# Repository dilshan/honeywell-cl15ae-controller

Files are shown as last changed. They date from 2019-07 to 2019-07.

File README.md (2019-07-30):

# Replacement driver for Honeywell CL15AE

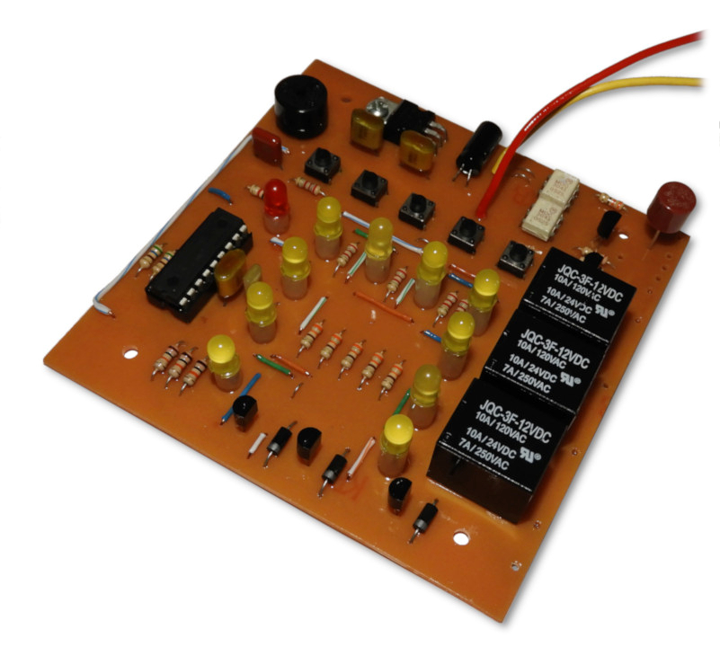
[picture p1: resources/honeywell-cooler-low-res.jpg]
Prototype version of the replacement board


PIC16F819 based replacement driver unit for Honeywell (JMTEK) CL15AE evaporative air cooler.

Detail posting about this project is available at [jayakody2000lk.blogspot.com](http://jayakody2000lk.blogspot.com/2019/07/replacement-driver-for-honeywell-cl15ae.html).

**WARNING:** This unit has a direct connection with the AC mains voltage and makes sure to take all necessary precautions while assembling, testing and installing this board. Improper connection or short-circuits would cause lethal shock or fire!

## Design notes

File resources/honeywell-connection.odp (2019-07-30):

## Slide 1

AC Mains Input

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
Main Motor

Swing Motor

Pump Motor

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
J5 / J7

J3 / J9

J13

J14

Control Board

PSU

N

L

Control board wiring diagram

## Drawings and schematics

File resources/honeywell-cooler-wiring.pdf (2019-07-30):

# Control Board

# Control board wiring diagram

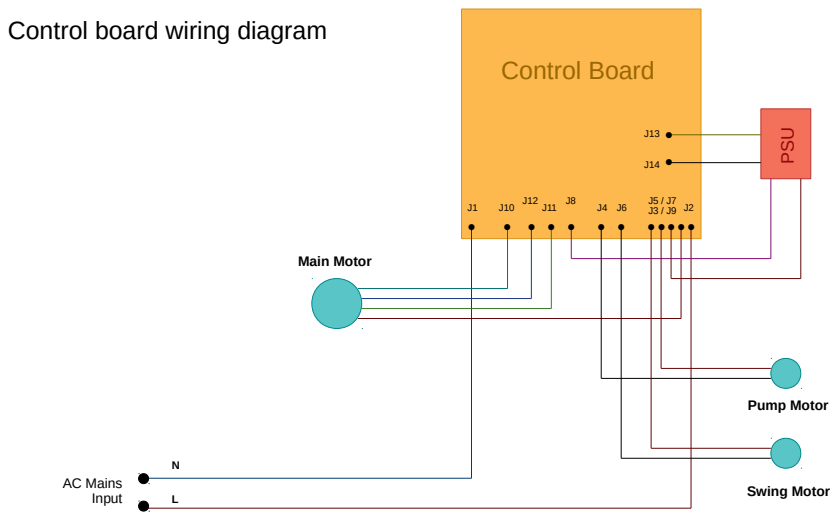
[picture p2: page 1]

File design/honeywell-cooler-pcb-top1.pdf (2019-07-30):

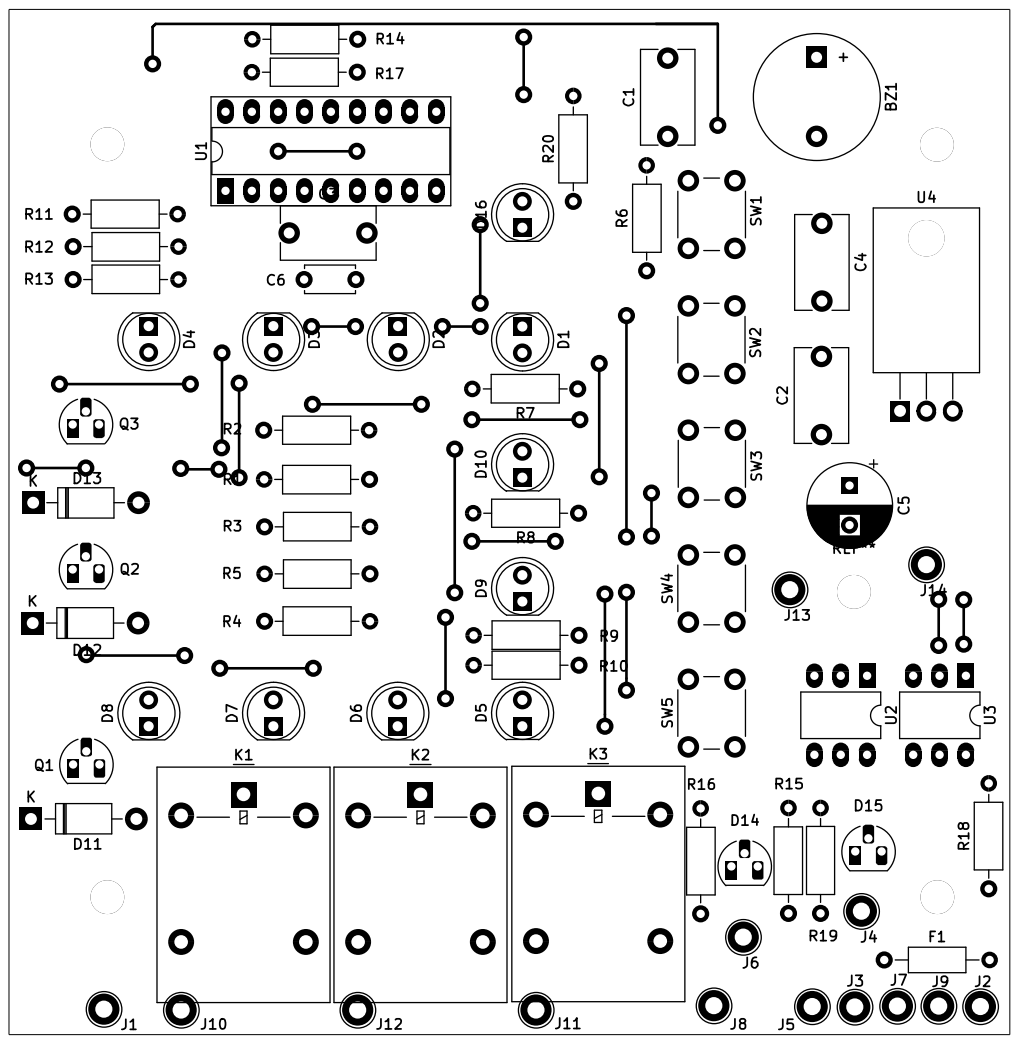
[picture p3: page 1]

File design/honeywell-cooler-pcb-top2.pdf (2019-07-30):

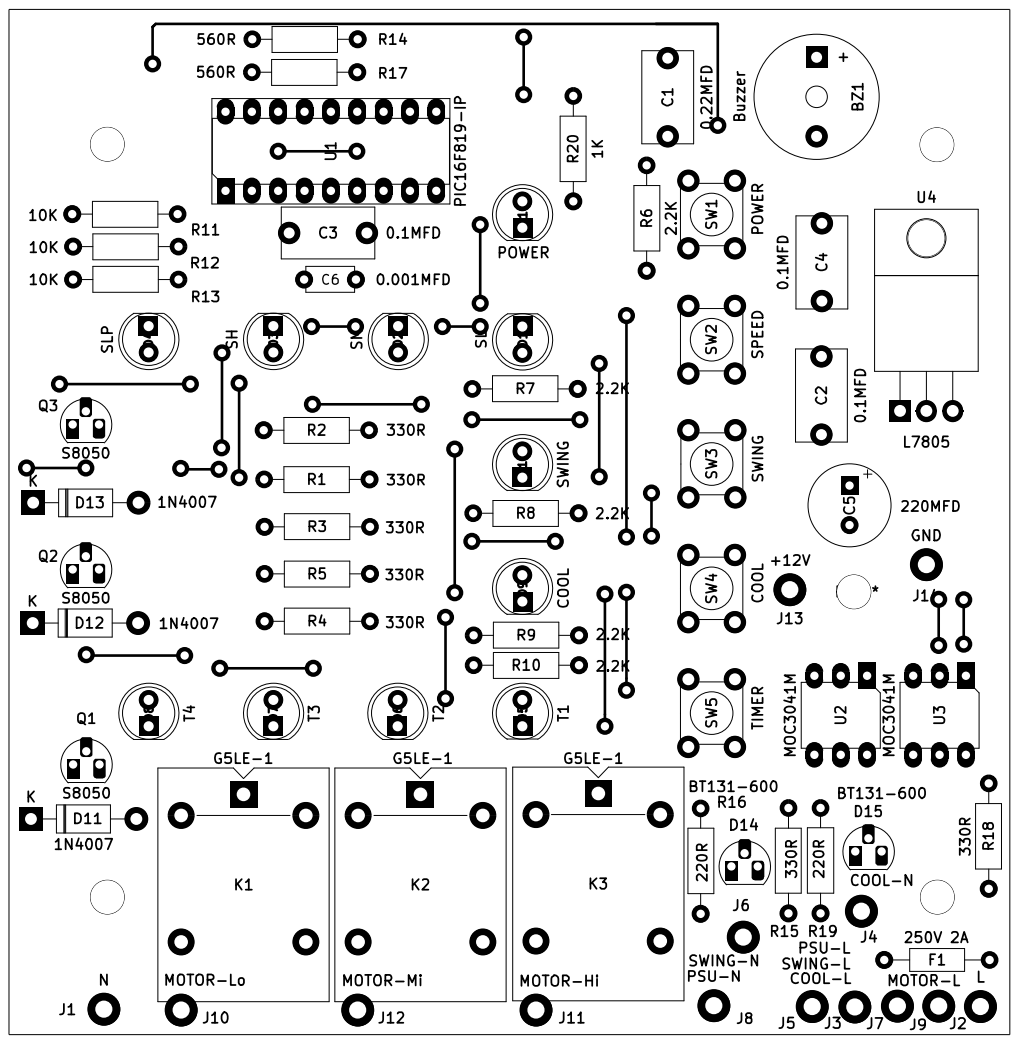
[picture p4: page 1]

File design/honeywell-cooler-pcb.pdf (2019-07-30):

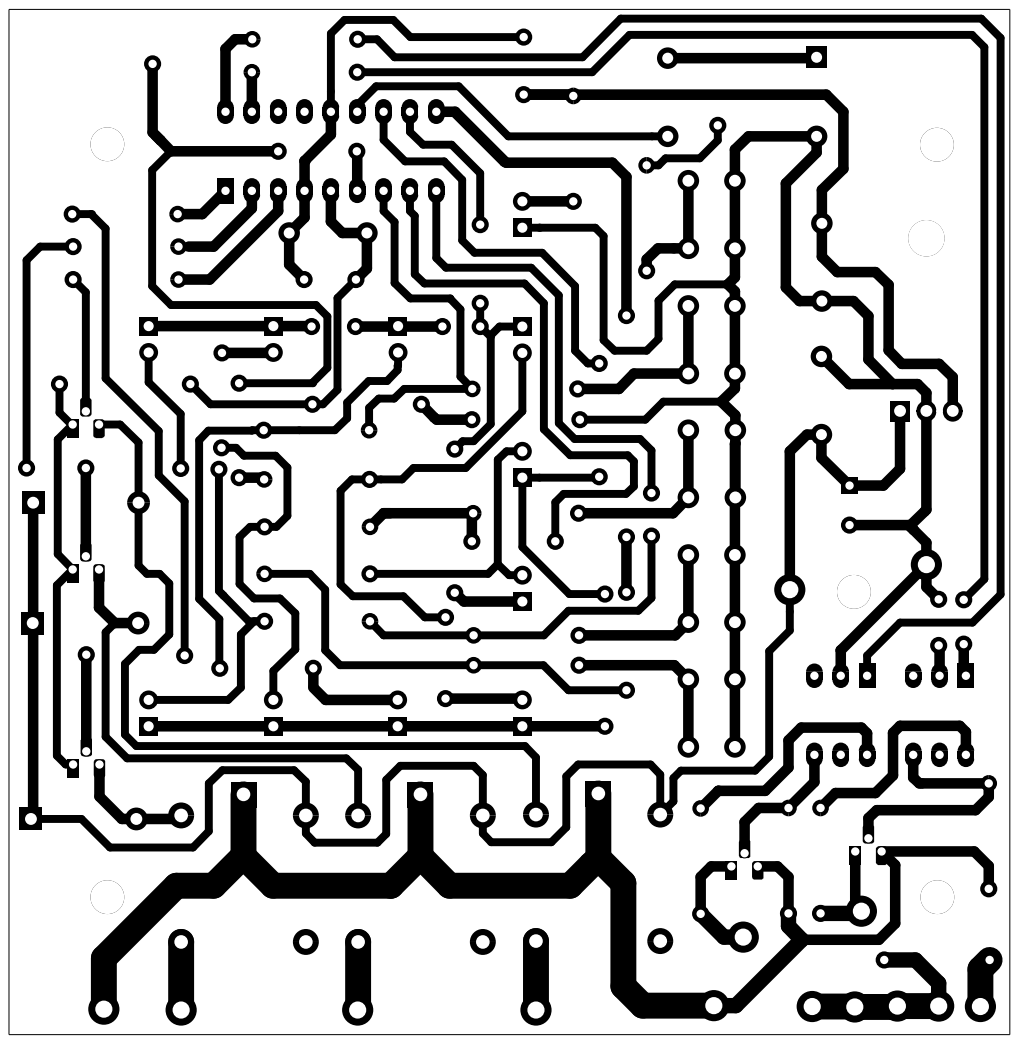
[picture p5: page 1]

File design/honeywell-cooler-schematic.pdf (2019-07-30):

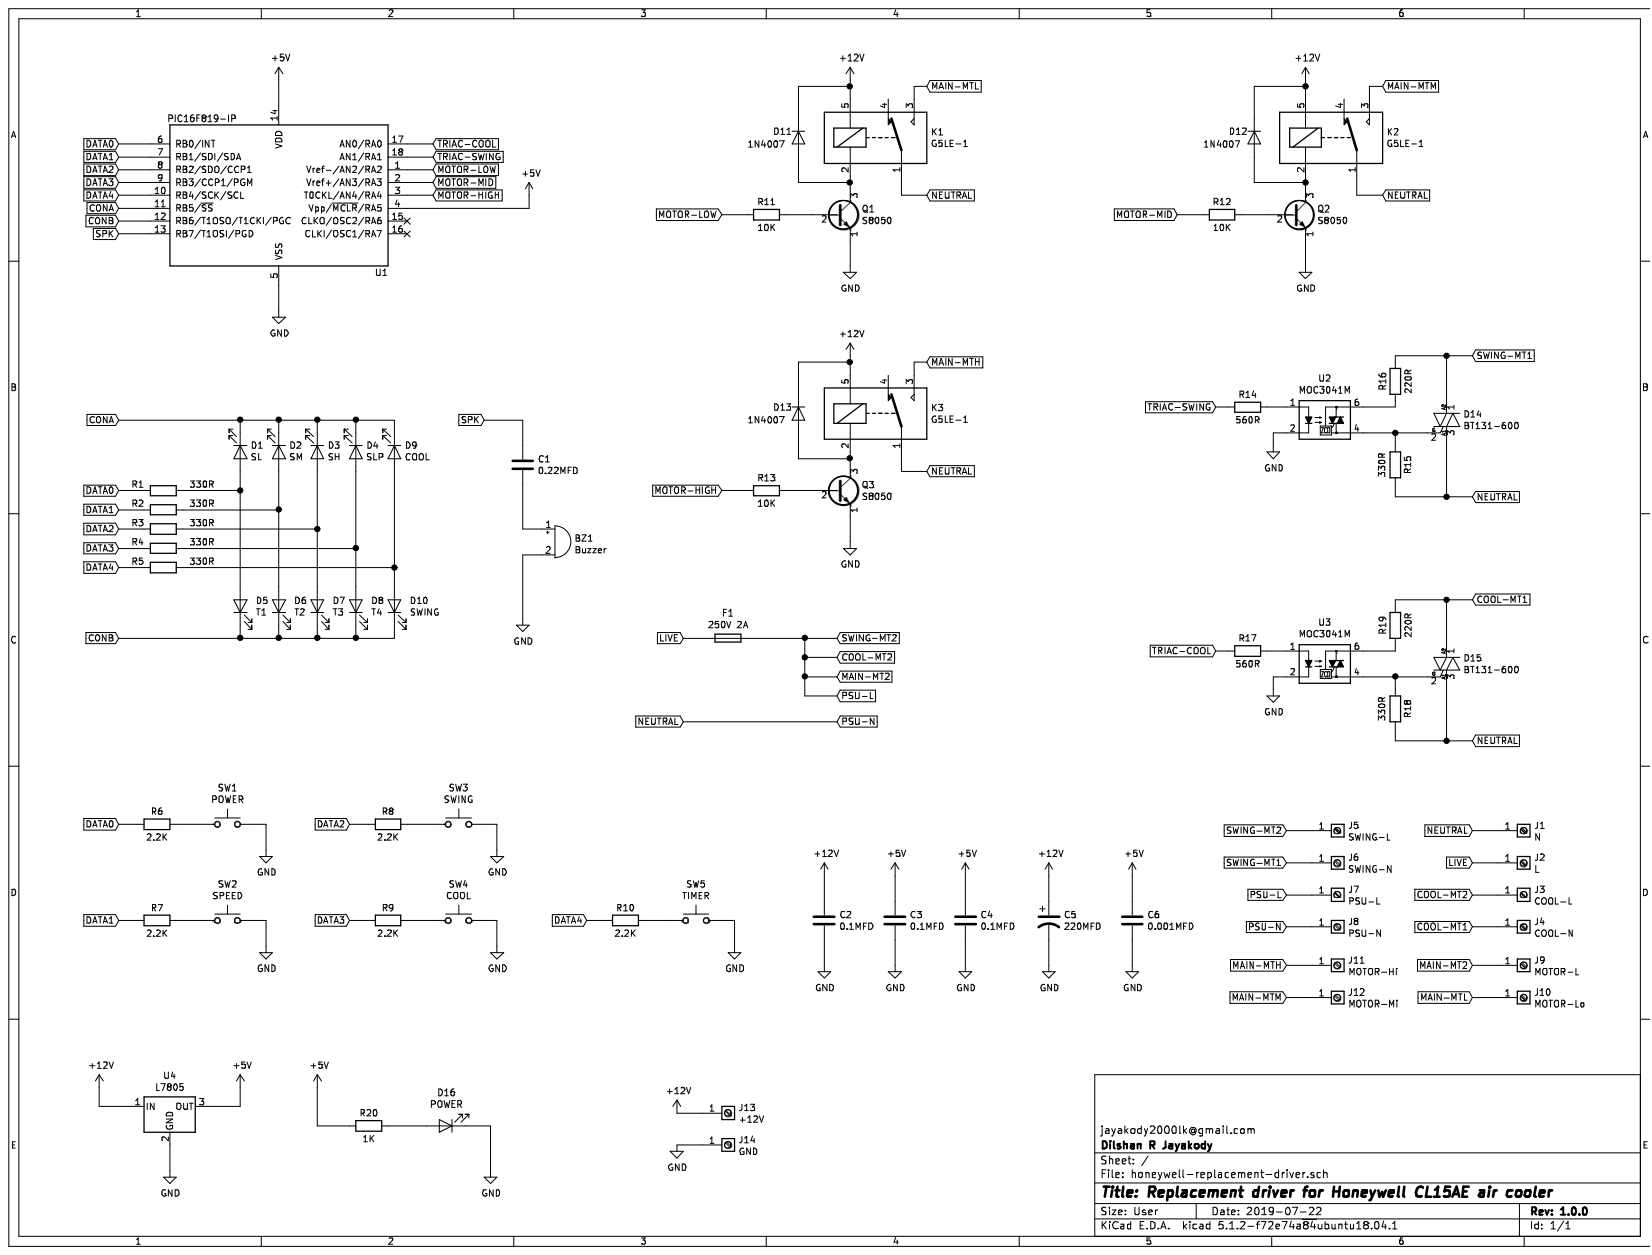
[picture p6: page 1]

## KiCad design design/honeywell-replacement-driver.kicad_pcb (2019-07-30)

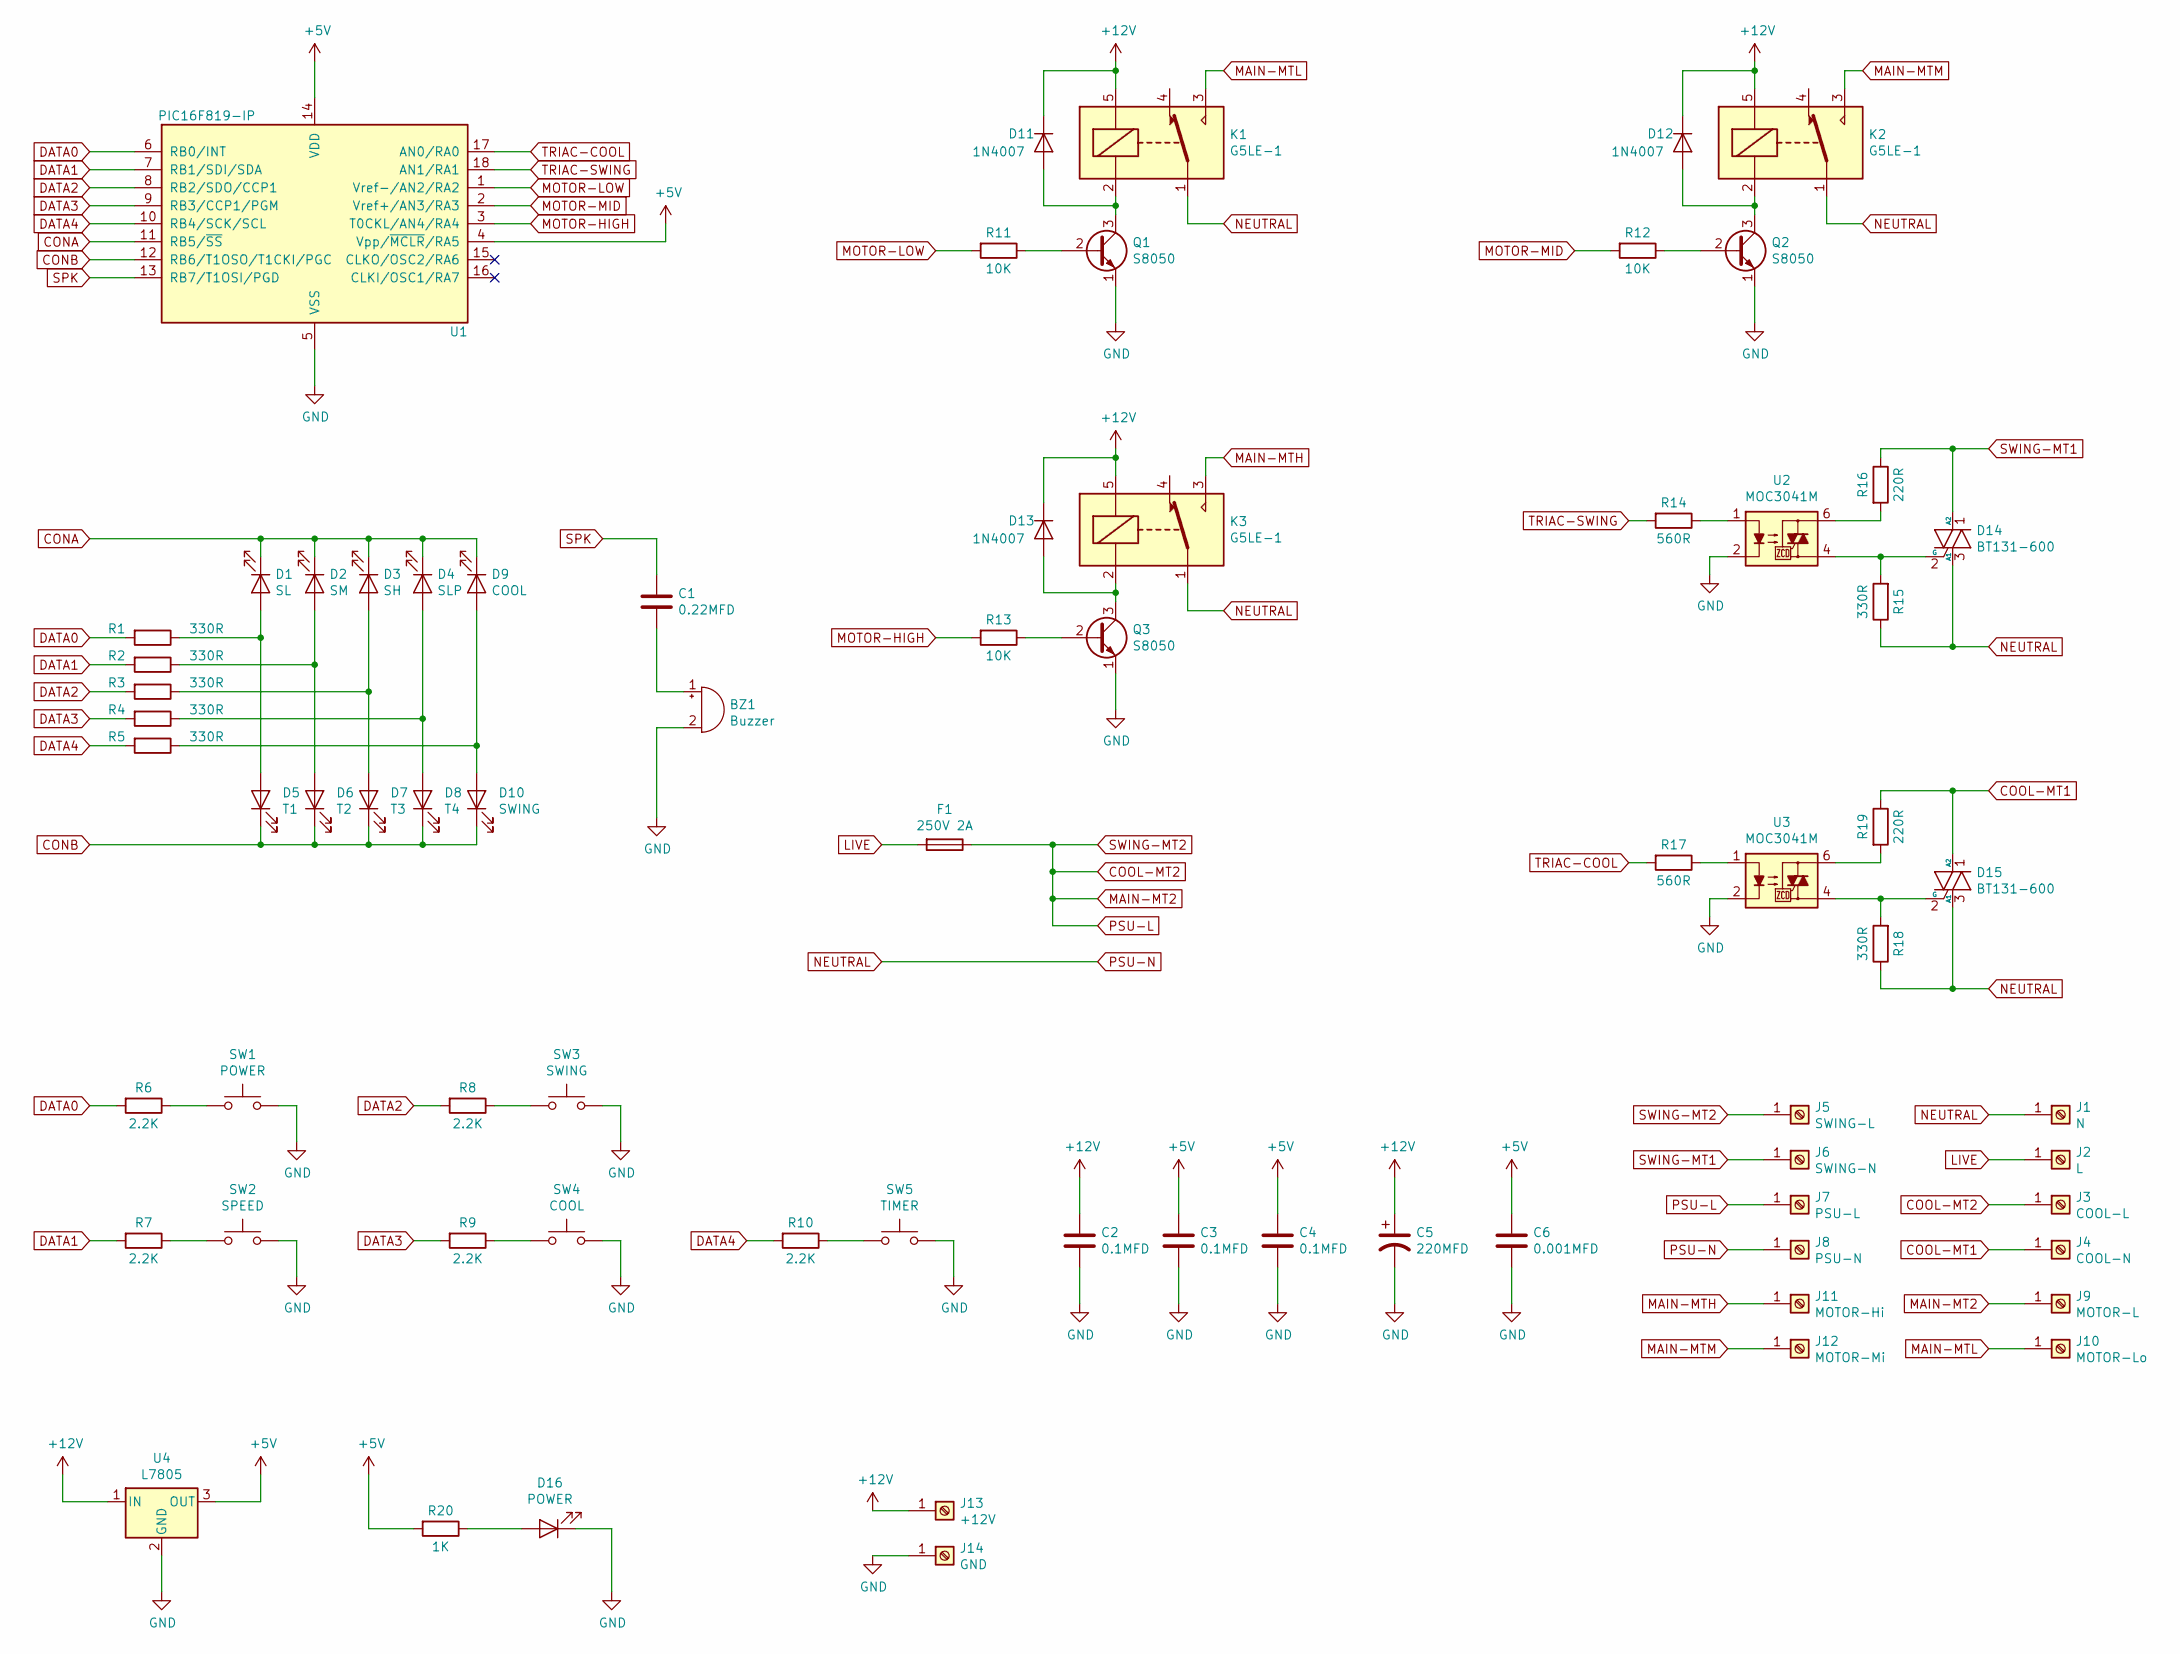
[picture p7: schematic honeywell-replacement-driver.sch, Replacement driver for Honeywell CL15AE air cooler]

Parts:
BZ1: Buzzer; Buzzer_12x9.5RM7.6
C1: 0.22MFD; C_Disc_D9.0mm_W5.0mm_P7.50mm
C2, C3, C4: 0.1MFD; C_Disc_D9.0mm_W5.0mm_P7.50mm
C5: 220MFD; CP_Radial_D8.0mm_P3.80mm
C6: 0.001MFD; C_Disc_D4.7mm_W2.5mm_P5.00mm
D1: SL; LED_D5.0mm
D2: SM; LED_D5.0mm
D3: SH; LED_D5.0mm
D4: SLP; LED_D5.0mm
D5: T1; LED_D5.0mm
D6: T2; LED_D5.0mm
D7: T3; LED_D5.0mm
D8: T4; LED_D5.0mm
D9: COOL; LED_D5.0mm
D10: SWING; LED_D5.0mm
D11, D12, D13: 1N4007; D_DO-41_SOD81_P10.16mm_Horizontal
D14, D15: BT131-600; TO-92_HandSolder
D16: POWER; LED_D5.0mm
F1: 250V 2A; L_Axial_L5.3mm_D2.2mm_P10.16mm_Horizontal_Vishay_IM-1
J1: N; TestPoint_Loop_D2.60mm_Drill1.6mm_Beaded
J2: L; TestPoint_Loop_D2.60mm_Drill1.6mm_Beaded
J3: COOL-L; TestPoint_Loop_D2.60mm_Drill1.6mm_Beaded
J4: COOL-N; TestPoint_Loop_D2.60mm_Drill1.6mm_Beaded
J5: SWING-L; TestPoint_Loop_D2.60mm_Drill1.6mm_Beaded
J6: SWING-N; TestPoint_Loop_D2.60mm_Drill1.6mm_Beaded
J7: PSU-L; TestPoint_Loop_D2.60mm_Drill1.6mm_Beaded
J8: PSU-N; TestPoint_Loop_D2.60mm_Drill1.6mm_Beaded
J9: MOTOR-L; TestPoint_Loop_D2.60mm_Drill1.6mm_Beaded
J10: MOTOR-Lo; TestPoint_Loop_D2.60mm_Drill1.6mm_Beaded
J11: MOTOR-Hi; TestPoint_Loop_D2.60mm_Drill1.6mm_Beaded
J12: MOTOR-Mi; TestPoint_Loop_D2.60mm_Drill1.6mm_Beaded
J13: +12V; TestPoint_Loop_D2.60mm_Drill1.6mm_Beaded
J14: GND; TestPoint_Loop_D2.60mm_Drill1.6mm_Beaded
K1, K2, K3: G5LE-1; Relay_SPDT_Omron-G5LE-1
Q1, Q2, Q3: S8050; TO-92_HandSolder
R1, R2, R3, R4, R5, R15, R18: 330R; R_Axial_DIN0207_L6.3mm_D2.5mm_P10.16mm_Horizontal
R6, R7, R8, R9, R10: 2.2K; R_Axial_DIN0207_L6.3mm_D2.5mm_P10.16mm_Horizontal
R11, R12, R13: 10K; R_Axial_DIN0207_L6.3mm_D2.5mm_P10.16mm_Horizontal
R14, R17: 560R; R_Axial_DIN0207_L6.3mm_D2.5mm_P10.16mm_Horizontal
R16, R19: 220R; R_Axial_DIN0207_L6.3mm_D2.5mm_P10.16mm_Horizontal
R20: 1K; R_Axial_DIN0207_L6.3mm_D2.5mm_P10.16mm_Horizontal
SW1: POWER; SW_PUSH_6mm
SW2: SPEED; SW_PUSH_6mm
SW3: SWING; SW_PUSH_6mm
SW4: COOL; SW_PUSH_6mm
SW5: TIMER; SW_PUSH_6mm
U1: PIC16F819-IP; DIP-18_W7.62mm_Socket_LongPads
U2, U3: MOC3041M; DIP-6_W7.62mm_LongPads
U4: L7805; TO-220-3_Horizontal_TabDown

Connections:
+5V: C3.1, C4.1, C6.1, R20.2, U1.4 (Vpp/~MCLR~/RA5), U1.14 (VDD), U4.3 (OUT)
+12V: C2.1, C5.1, D11.1 (K), D12.1 (K), D13.1 (K), J13.1, K1.5, K2.5, K3.5, U4.1 (IN)
CONA: D1.1 (K), D2.1 (K), D3.1 (K), D4.1 (K), D9.1 (K), U1.11 (RB5/~SS~)
CONB: D5.1 (K), D6.1 (K), D7.1 (K), D8.1 (K), D10.1 (K), U1.12 (RB6/T1OSO/T1CKI/PGC)
COOL-MT1: D15.1 (A2), J4.1, R19.1
COOL-MT2: F1.1, J3.1, J5.1, J7.1, J9.1
DATA0: R1.2, R6.2, U1.6 (RB0/INT)
DATA1: R2.2, R7.2, U1.7 (RB1/SDI/SDA)
DATA2: R3.2, R8.2, U1.8 (RB2/SDO/CCP1)
DATA3: R4.2, R9.2, U1.9 (RB3/CCP1/PGM)
DATA4: R5.2, R10.2, U1.10 (RB4/SCK/SCL)
GND: BZ1.2 (+), C2.2, C3.2, C4.2, C5.2, C6.2, D16.1 (K), J14.1, Q1.1 (E), Q2.1 (E), Q3.1 (E), SW1.2, SW2.2, SW3.2, SW4.2, SW5.2, U1.5 (VSS), U2.2, U3.2, U4.2 (GND)
LIVE: F1.2, J2.1
MAIN-MTH: J11.1, K3.3
MAIN-MTL: J10.1, K1.3
MAIN-MTM: J12.1, K2.3
MOTOR-HIGH: R13.2, U1.3 (T0CKL/AN4/RA4)
MOTOR-LOW: R11.2, U1.1 (Vref-/AN2/RA2)
MOTOR-MID: R12.2, U1.2 (Vref+/AN3/RA3)
NEUTRAL: D14.3 (A1), D15.3 (A1), J1.1, J8.1, K1.1, K2.1, K3.1, R15.1, R18.1
unnamed: BZ1.1 (-), C1.2
unnamed: D1.2 (A), D5.2 (A), R1.1
unnamed: D2.2 (A), D6.2 (A), R2.1
unnamed: D3.2 (A), D7.2 (A), R3.1
unnamed: D4.2 (A), D8.2 (A), R4.1
unnamed: D9.2 (A), D10.2 (A), R5.1
unnamed: D11.2 (A), K1.2, Q1.3 (C)
unnamed: D12.2 (A), K2.2, Q2.3 (C)
unnamed: D13.2 (A), K3.2, Q3.3 (C)
unnamed: D14.2 (G), R15.2, U2.4
unnamed: D15.2 (G), R18.2, U3.4
unnamed: D16.2 (A), R20.1
unnamed: Q1.2 (B), R11.1
unnamed: Q2.2 (B), R12.1
unnamed: Q3.2 (B), R13.1
unnamed: R6.1, SW1.1
unnamed: R7.1, SW2.1
unnamed: R8.1, SW3.1
unnamed: R9.1, SW4.1
unnamed: R10.1, SW5.1
unnamed: R14.1, U2.1
unnamed: R16.2, U2.6
unnamed: R17.1, U3.1
unnamed: R19.2, U3.6
SPK: C1.1, U1.13 (RB7/T1OSI/PGD)
SWING-MT1: D14.1 (A2), J6.1, R16.1
TRIAC-COOL: R17.2, U1.17 (AN0/RA0)
TRIAC-SWING: R14.2, U1.18 (AN1/RA1)

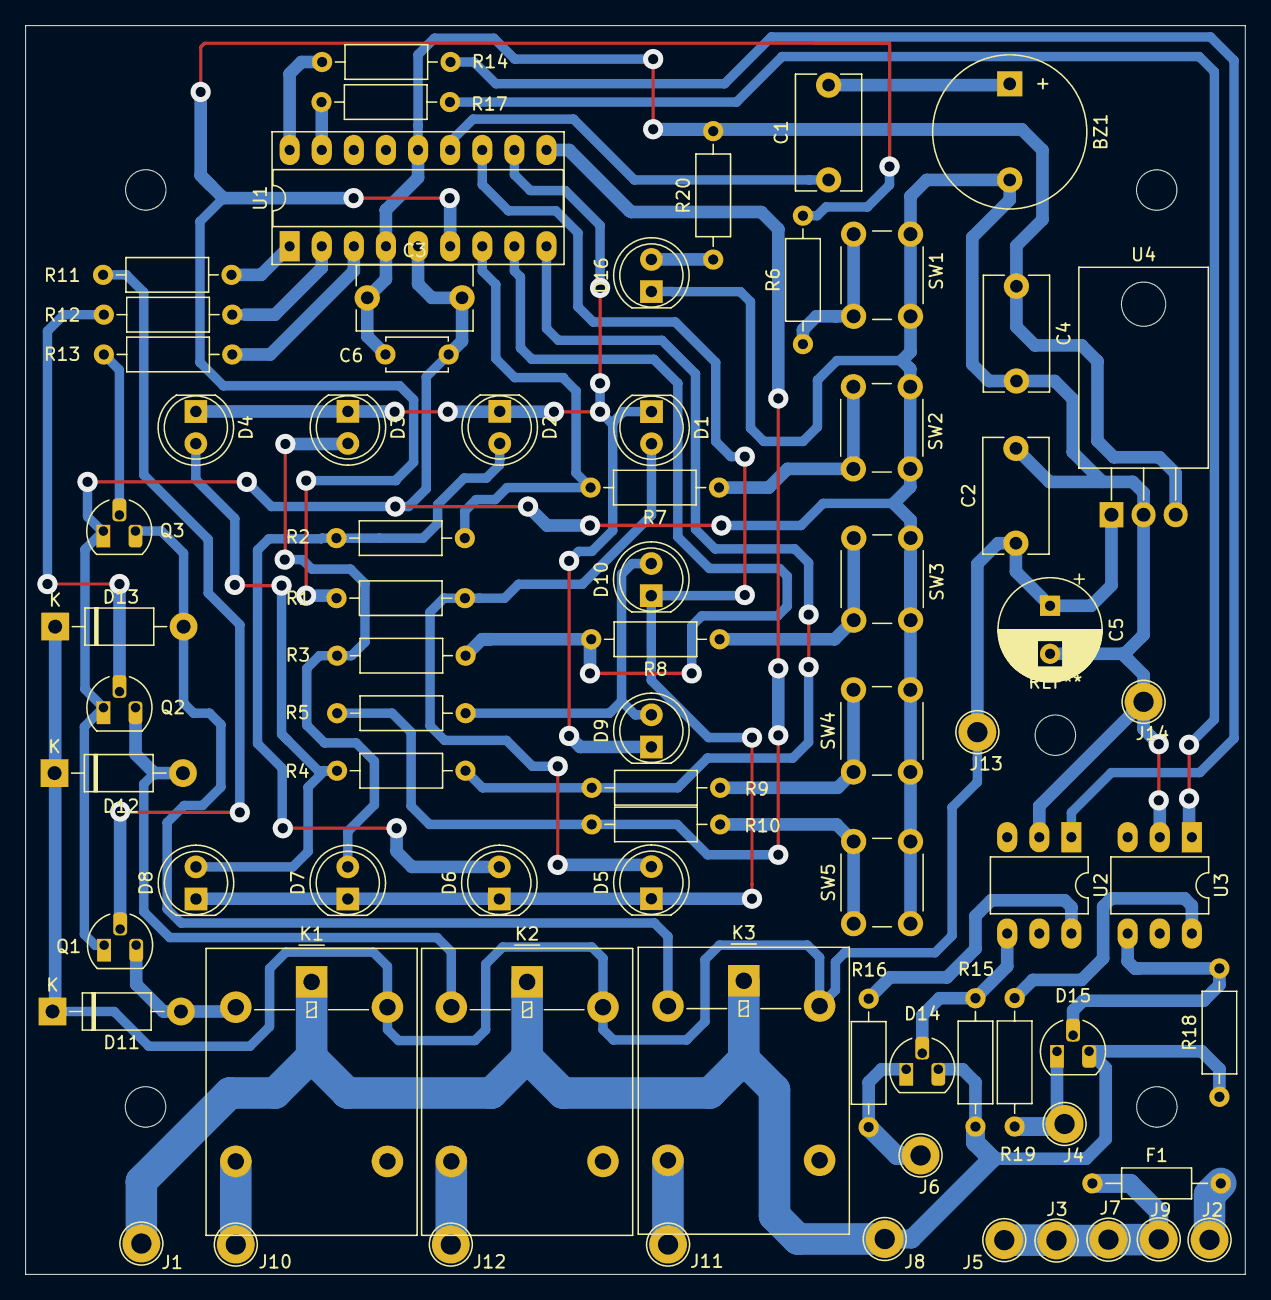
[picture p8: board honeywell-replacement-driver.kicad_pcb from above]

Board: 2 copper layers, 96.5 x 98.8 mm, 77 parts (0 on the bottom side), 48 nets.

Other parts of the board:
 : MountingHole_3.2mm_M3
 #2,  #3,  #4: MountingHole_3.2mm_M3

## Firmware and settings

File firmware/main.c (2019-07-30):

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
#include "main.h"
#include "memory.h"

int main() 
{
    unsigned char mainButtonState = 0x00;
    unsigned char lastButtonState = 0x00;
    
    // Initialize global variables.
    mainConfig.flag = 0;
    mainConfig.speed = 1;
    mainConfig.timer = 0;
    
    timerVal = 0;
    timerTarget = 0;
    buttonIgnore = 0;
    
    sysState = MS_IDLE;
    
    // Start Initialize the system.
    initSystem();
    readEEPROM(&mainConfig);
    activateBuzzer();
    
    // Idle service loop.
    while(1)
    {
        if(buttonIgnore == 0)
        {
            scanButtonState(&mainButtonState);
        }
        else
        {
            // Ignore switch bouncing.
            if((++buttonIgnore) == BUTTON_IGNORE_LIMIT)
            {
                buttonIgnore = 0;
            }
        }
        
        if(((mainButtonState & BTN_POWER) == 0x00) && ((lastButtonState & BTN_POWER) == BTN_POWER))
        {
            // Turn on the system.
            buttonIgnore = 1;
            activateBuzzer();
            mainConfig.flag = mainConfig.flag | CONFIG_FLAG_POWER;
            
            __delay_ms(10);
            mainService();
            
            readEEPROM(&mainConfig);
            mainButtonState = 0x00;
        }
        
        lastButtonState = mainButtonState;
        __delay_ms(10);
    }
    
    return 0;
}

void updateIndicators(const sysConfig *config)
{
    TRISB = 0x00;
    
    // Update speed indicators.
    PORTB = PORTB & 0x80;
    PORTB = PORTB | (config->speed) | 0x40;
    __delay_ms(1);
    
    // Update timer indicators.
    PORTB = PORTB & 0x80;
    PORTB = PORTB | (config->timer) | 0x20;
    __delay_ms(1);
    
    // Update cool indicator.
    PORTB = PORTB & 0x80;
    if((config->flag) & CONFIG_FLAG_COOL)
    {
        PORTB = PORTB | 0x50;
    }
    __delay_ms(1);

    // Update swing indicator.
    PORTB = PORTB & 0x80;
    if((config->flag) & CONFIG_FLAG_SWING)
    {
        PORTB = PORTB | 0x30;
    }
    __delay_ms(1);
    
    PORTB = PORTB & 0x80;
}

void shutdownSystem()
{    
    // Shutdown indicators.
    PORTB = 0x60;
    TRISB = 0x00;
    
    // Shutdown all motors in the system.
    PORTA = 0x00;
}

void scanButtonState(unsigned char *buttonState)
{
    unsigned char tempButtonState = 0x00;
    
    PORTB = 0x60;
    TRISB = 0x1F;
    
    // Check state of the POWER button.
    if(!(PORTBbits.RB0))
    {
        tempButtonState = tempButtonState | BTN_POWER;
    }
    
    // Check state of the SPEED button.
    if(!(PORTBbits.RB1))
    {
        tempButtonState = tempButtonState | BTN_SPEED;
    }
    
    // Check state of the SWING button.
    if(!(PORTBbits.RB2))
    {
        tempButtonState = tempButtonState | BTN_SWING;
    }
    
    // Check state of the COOL button.
    if(!(PORTBbits.RB3))
    {
        tempButtonState = tempButtonState | BTN_COOL;
    }
    
    // Check state of the TIMER button.
    if(!(PORTBbits.RB4))
    {
        tempButtonState = tempButtonState | BTN_TIMER;
    }
    
    PORTB = 0x60;
    TRISB = 0x00;
    
    *buttonState = tempButtonState;
}

void activateBuzzer()
{
    unsigned char bellCounter = 254;
    TRISB = TRISB & 0x7F;
    
    while((--bellCounter) > 0)
    {
        // Generate 2kHz waveform on PORTB7.
        PORTBbits.RB7 = (bellCounter % 2);
        __delay_us(200);
    }  
    
    // Reset PORTB7 and shutdown buzzer.
    PORTBbits.RB7 = 0;
}

void commitConfig(const MotorState execState)
{
    sysState = execState;
    
    // Switch system to specified state in 100ms.
    TMR0 = 60;
    INTCONbits.TMR0IE = 1;
    INTCONbits.TMR0IF = 0;
}

void enableSleepTimer(unsigned char timeSlot)
{
    if(timeSlot > 0)
    {
        // Enable sleep timer with 2sec interval.
        timerTarget = 900 * timeSlot;
        timerVal = 0;

        PIR1bits.TMR1IF = 0;
        PIE1bits.TMR1IE = 1;

        T1CON = 0x31;
        TMR1H = 0x0B;
        TMR1L = 0xDC;
    }
    else
    {
        // Disable sleep timer and clear flags.
        T1CON = 0x00;
        PIR1bits.TMR1IF = 0;
        PIE1bits.TMR1IE = 0;
        
        timerVal = 0;
        timerTarget = 0;
        
        mainConfig.flag = mainConfig.flag & (~CONFIG_FLAG_SLEEP);
    }
}

void initSystem()
{
    // Setup MCU clock to 1MHz.
    OSCCON = 0x40;
    
    // Configure MCU peripherals and system registers.
    ADCON0 = 0x00;
    ADCON1 = 0x06;
    CCP1CON = 0x00;
    SSPCON = 0x05;
    OPTION_REG = 0x46;
    INTCON = 0xC0;
    T1CON = 0x00;
    
    // Set I/O port values to default state.
    TRISB = 0x00;
    PORTB = 0x60;
    
    TRISA = 0x00;
    PORTA = 0x00;
}

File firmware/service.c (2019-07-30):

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
#include "main.h"
#include "memory.h"

void mainService()
{
    unsigned char mainButtonState = 0x00;
    unsigned char lastButtonState = 0x00;
    
    commitConfig(MS_MAIN_MOTOR);
    
    while(!((mainConfig.flag) & CONFIG_FLAG_SLEEP))
    {
        if(buttonIgnore == 0)
        {
            scanButtonState(&mainButtonState);
        }
        else
        {
            // Ignore switch bouncing.
            if((++buttonIgnore) == BUTTON_IGNORE_LIMIT)
            {
                buttonIgnore = 0;
            }
        }
        
        // Check for POWER button event.
        if(((mainButtonState & BTN_POWER) == 0x00) && ((lastButtonState & BTN_POWER) == BTN_POWER))
        {
            // Shutdown the system
            buttonIgnore = 1;
            mainConfig.flag = mainConfig.flag & (~(CONFIG_FLAG_POWER | CONFIG_FLAG_SLEEP));
            shutdownSystem();
            break;
        }
        
        // Check for SPEED button event.
        if(((mainButtonState & BTN_SPEED) == 0x00) && ((lastButtonState & BTN_SPEED) == BTN_SPEED))
        {
            mainConfig.speed = mainConfig.speed << 1;
            if(mainConfig.speed > 4)
            {
                mainConfig.speed = 1;
            }
            
            commitConfig(MS_MAIN_MOTOR);
            writeEEPROM(&mainConfig);
            buttonIgnore = 1;
        }
        
        // Check for TIMER button event.
        if(((mainButtonState & BTN_TIMER) == 0x00) && ((lastButtonState & BTN_TIMER) == BTN_TIMER))
        {
            if(mainConfig.timer == 0)
            {
                mainConfig.timer = 1;
            }
            else
            {
                mainConfig.timer = mainConfig.timer << 1;
                if(mainConfig.timer > 8)
                {
                    mainConfig.timer = 0;
                }
            }
            
            enableSleepTimer(mainConfig.timer);
            buttonIgnore = 1;
        }
        
        // Check for COOL button event.
        if(((mainButtonState & BTN_COOL) == 0x00) && ((lastButtonState & BTN_COOL) == BTN_COOL))
        {
            if((mainConfig.flag & CONFIG_FLAG_COOL) == CONFIG_FLAG_COOL)
            {
                mainConfig.flag = mainConfig.flag & (~CONFIG_FLAG_COOL);
            }
            else
            {
                mainConfig.flag = mainConfig.flag | CONFIG_FLAG_COOL;
            }
            
            commitConfig(MS_COOLER);
            writeEEPROM(&mainConfig);
            buttonIgnore = 1;
        }
        
        // Check for SWING button event.
        if(((mainButtonState & BTN_SWING) == 0x00) && ((lastButtonState & BTN_SWING) == BTN_SWING))
        {
            if((mainConfig.flag & CONFIG_FLAG_SWING) == CONFIG_FLAG_SWING)
            {
                mainConfig.flag = mainConfig.flag & (~CONFIG_FLAG_SWING);
            }
            else
            {
                mainConfig.flag = mainConfig.flag | CONFIG_FLAG_SWING;
            }
            
            commitConfig(MS_SWING);
            writeEEPROM(&mainConfig);
            buttonIgnore = 1;
        }
        
        // Update front panel indicators with current system configuration.
        updateIndicators(&mainConfig);
        lastButtonState = mainButtonState;
        __delay_ms(5);
    }
    
    if((mainConfig.flag) & CONFIG_FLAG_SLEEP)
    {
        PORTB = 0x60;
        TRISB = 0x00;
        
        sleepService();
    }
}

void sleepService()
{
    unsigned char mainButtonState = 0x00;
    unsigned char lastButtonState = 0x00;
    
    buttonIgnore = 0;
    
    while(1)
    {
        scanButtonState(&mainButtonState);
        
        // Check for POWER button event.
        if(((mainButtonState & BTN_POWER) == 0x00) && ((lastButtonState & BTN_POWER) == BTN_POWER))
        {
            mainConfig.flag = mainConfig.flag & (~(CONFIG_FLAG_POWER | CONFIG_FLAG_SLEEP));
            shutdownSystem();
            buttonIgnore = 1;
            break;
        }
        
        TRISB = 0x00;
        PORTB = PORTB & 0x80;
        PORTB = PORTB | 0x48;
        __delay_ms(1);
        PORTB = PORTB & 0x80;
        
        lastButtonState = mainButtonState;
        __delay_ms(5);
    }
}

void __interrupt() mainISR()
{
    if((INTCONbits.TMR0IE) && (INTCONbits.TMR0IF)) 
    {
        if((mainConfig.flag & CONFIG_FLAG_POWER) == 0x00)
        {
            // Shutdown all the motors in the system.
            PORTA = 0x00;
            sysState = MS_IDLE;
            INTCONbits.TMR0IE = 0;
        }
        else
        {
            // Handle main motor (speed) state.
            if(sysState == MS_MAIN_MOTOR)
            {
                PORTA = (PORTA & 0xE3) | (mainConfig.speed << 2);
            }
            
            // Handle cooler pump state.
            if(sysState == MS_COOLER)
            {
                PORTA = PORTA & 0xFE;
                if(mainConfig.flag & CONFIG_FLAG_COOL)
                {
                    PORTA = PORTA | 0x01;
                }
            }
            
            // Handle swing motor state.
            if(sysState == MS_SWING)
            {
                PORTA = PORTA & 0xFD;
                if(mainConfig.flag & CONFIG_FLAG_SWING)
                {
                    PORTA = PORTA | 0x02;
                }
            }
            
            // Move to next available state.
            intrMoveToNextState(sysState);
        }
    }
    else if((PIE1bits.TMR1IE) && (PIR1bits.TMR1IF))
    {
        timerVal++;
        
        if(timerVal >= timerTarget)
        {
            mainConfig.flag = mainConfig.flag | CONFIG_FLAG_SLEEP;
            PORTA = 0x00;
            T1CON = 0x00;
            PIE1bits.TMR1IE = 0;
        }
        else
        {
            TMR1H = 0x0B;
            TMR1L = 0xDC;
            PIE1bits.TMR1IE = 1;
        }
        
        PIR1bits.TMR1IF = 0;
    }
}

void intrMoveToNextState(const MotorState execState)
{
    switch(execState)
    {
        case MS_IDLE:
            INTCONbits.TMR0IE = 0;
            INTCONbits.TMR0IF = 0;
            return;
        case MS_MAIN_MOTOR:
            sysState = MS_COOLER;
            break;
        case MS_COOLER:
            sysState = MS_SWING;
            break;
        case MS_SWING:
            sysState = MS_IDLE;
            break;
    }
    
    // Switch system to specified state in 50ms.
    TMR0 = 157;
    INTCONbits.TMR0IE = 1;
    INTCONbits.TMR0IF = 0;
}

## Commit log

2019-07-30 Initial version of the project.
    [honeywell-replacement-driver.kicad_pcb, honeywell-replacement-driver.sch]
2019-07-30 Update readme file with prototype board.

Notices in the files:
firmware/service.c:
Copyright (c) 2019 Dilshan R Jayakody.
